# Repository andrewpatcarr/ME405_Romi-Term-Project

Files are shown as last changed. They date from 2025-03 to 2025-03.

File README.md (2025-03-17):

# ME-405 Romi Term Project
### By: Andrew Carr and Alain Kanadjian
### Instructor: Charlie Refvem

---

This repository houses all documentation regarding our Romi project 
that was worked on throughout this quarter.

All documentation can be found here:

[ME-405 Romi Term Project Documentation](https://andrewpatcarr.github.io/ME405_Romi-Term-Project/)

### The Project

Throughout our quarter in ME-405, we worked on labs that used our mini-car robot, Romi, in different ways. 
We parameterized our motors, implemented task-based non-blocking programming, implemented an IR line sensor, and worked with an IMU. 
All of these labs were building towards our term project/challenge.

romi_pic

We were tasked with completing a complex track with obstacles, quick bends, and varying surface prints. 

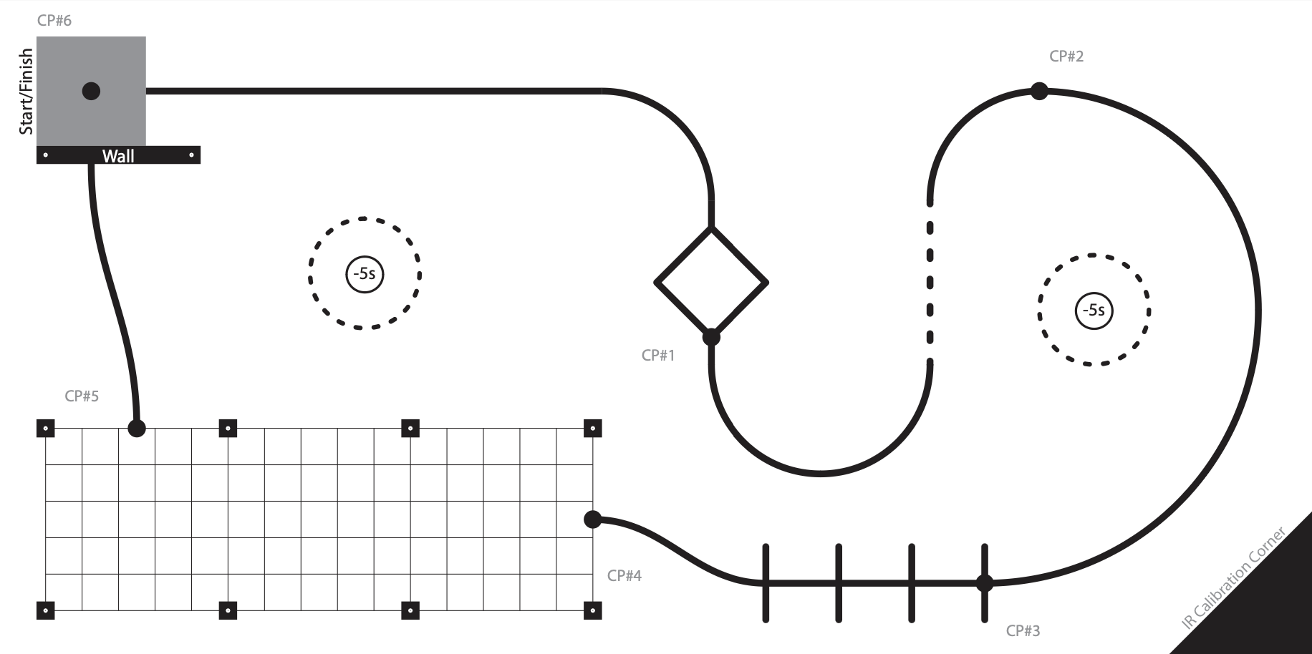
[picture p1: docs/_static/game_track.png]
Game Track


### Hardware

Our Pololu Romi has a STM-32 Nucleo with a Calpoly custom 'Shoe of Brian' along with a Pololu motor driver.

Romi has two DC motor driven wheels with quadrature encoders. We mounted an IMU for orientation sensing, 
an IR sensor to track a black line, and a bump sensor for impact sensing.

See cad and pinout folders for files and the [hardware](https://andrewpatcarr.github.io/ME405_Romi-Term-Project/hardware.html)
and [assembly](https://andrewpatcarr.github.io/ME405_Romi-Term-Project/assembly.html) pages for documentation.

### Programming

We structured our code using object-oriented programming principles and task-based architecture for
streamlined modifications and control. Each part of the robot runs as a separate task, allowing for easy 
debugging and organization. We use a PI controller to set motor speed based on encoder feedback. 
The encoder uses quadrature signals and an AR reset to prevent overflow. Our IR sensor uses a centroid-based 
algorithm to track black lines for navigation.

See the source code in the code folder and the [programming](https://andrewpatcarr.github.io/ME405_Romi-Term-Project/programming.html),
[control](https://andrewpatcarr.github.io/ME405_Romi-Term-Project/control_scheme.html), and
[code modules](https://andrewpatcarr.github.io/ME405_Romi-Term-Project/code_rst/modules.html) pages for detailed documentation.

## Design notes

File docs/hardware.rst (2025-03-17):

Hardware
========

Components
----------

.. list-table::
   :widths: 50 20 50
   :header-rows: 1

   * - Item
     - Quantity
     - Notes
   * - `Romi Chassis Kit <https://www.pololu.com/category/203/romi-chassis-kits>`_
     - 1
     - A differential-drive mobile robot platform.
   * - `Romi Ball Caster Kit <https://www.pololu.com/category/204/romi-chassis-components>`_
     - 1
     - Provides a third point of contact for the robot.
   * - `Snap-Action Switch with 18.5mm Bump Lever <https://www.pololu.com/product/1405>`_
     - 1
     - A single-pole, double-throw momentary switch used as a tactile bump sensor for physical collisions.
   * - `QTR-HD-13A Reflectance Sensor Array <https://www.pololu.com/product/4213>`_
     - 1
     - A 13-channel array of IR LED/phototransistor pairs with 4mm length, used for precise line detection and following.
   * - `Gearmotor and Encoder Assembly for Romi/TI-RSLK MAX <https://www.pololu.com/product/3675>`_
     - 2
     -  Gearmotors with encoders pre-installed, providing feedback for precise motor control
   * - `Adafruit BNO055 IMU <https://learn.adafruit.com/adafruit-bno055-absolute-orientation-sensor/overview>`_
     - 1
     - 9-DOF absolute orientation sensor
   * - `STM32 NUCLEO-L476RG <https://www.st.com/en/evaluation-tools/nucleo-l476rg.html>`__
     - 1
     - Microcontroller Dev Board

Romi
----
Romi is a small differential drive robot that uses two wheels powered by DC
motors with encoders. Romi has a Shoe of Brian and Nucleo-L476RG along with
attached components like a bump sensor, QTR sensor, and IMU. The plastic
chassis is lightweight allowing easier configuration and navigation. The
two DC motors are connected to a gearbox for proper torque, controlled by
pulse width modulation signals, allowing for variable speed control. The
encoders connected to the motors allow for a closed feedback loop, so we
can implement motion tracking and autonomous movement. The motor driver
controls the voltage and current to each motor, allowing for bidirectional
movement and speed control.

To help control each motor, we ran step input tests to find different characteristics of the motors.

Example Plots (Right Motor)
---------------------------

Position vs Time at different open loop step inputs

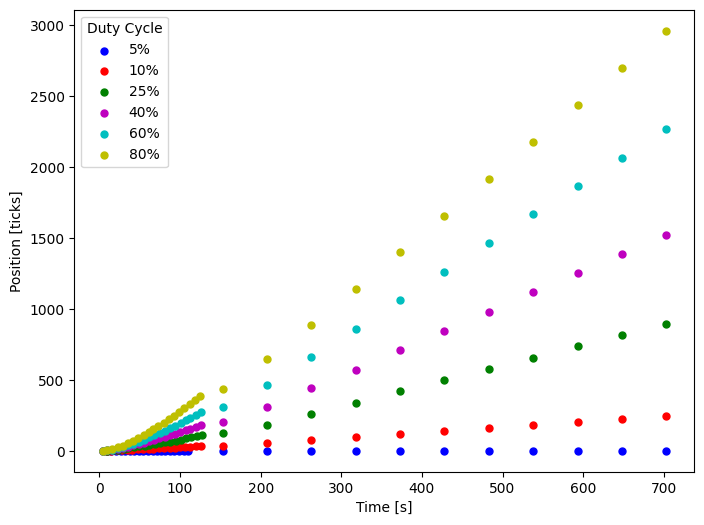
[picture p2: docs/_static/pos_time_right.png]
pos_time_right


Velocity vs Time at different open loop step inputs

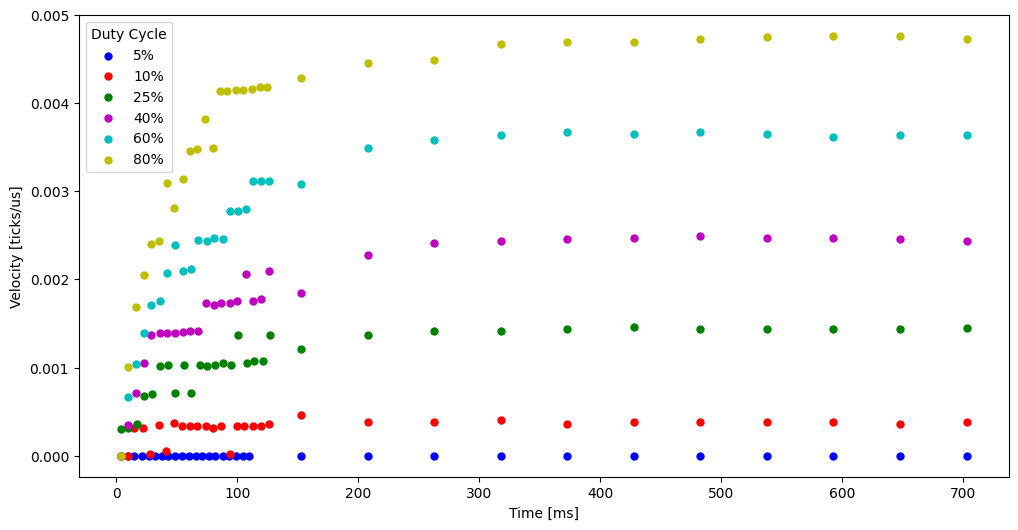
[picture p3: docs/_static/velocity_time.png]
velocity_time


Steady-State Velocity vs Input Voltage

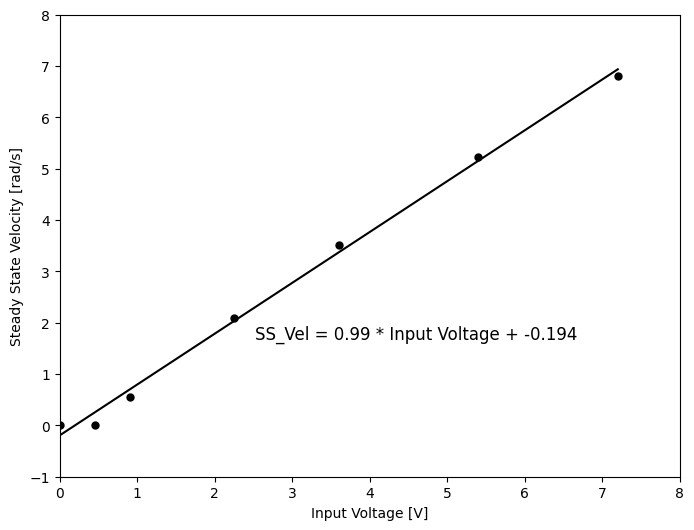
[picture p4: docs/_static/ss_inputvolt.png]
ss_inputvolt


Linearized Velocity vs Time (inverse of slope gives time constant)

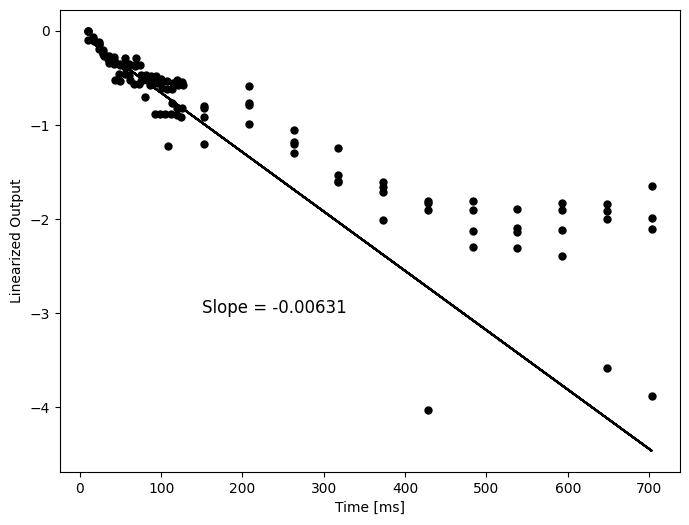
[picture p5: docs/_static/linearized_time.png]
linearized_time


Motor Parameters
----------------

.. list-table::
   :widths: 20 40 30 40
   :header-rows: 1

   * - Motor
     - Time Constant [ms]
     - Gain [deg/s]
     - Startup PWM %
   * - Right
     - 158
     - 56.7
     - 2.77
   * - Left
     - 170
     - 60.3
     - 6.48

STM-32 Nucleo
-------------
Our Romi uses a STM32 Nucleo (particularly the `NUCLEO-L476RG <https://www.st.com/en/evaluation-tools/nucleo-l476rg.html>`_)
as its microcontroller. The board has an ARM processor, various GPIO pins,
and interfaces for I2C, SPI, and UART. The Nucleo allows for real time data processing, sensor
integration and motor control through MicroPython.

QTR Sensor
----------
The QTR sensor has an array of infrared reflectance sensor for line following, consisting of an IR LED
and phototransistor to detect reflectance of the surface it is pointed at. White surfaces return low readings,
while black surfaces return high readings. This sensor helps ROMI implement PID line following, adjusting motor
speeds based on intensity of reflected light to the sensor.

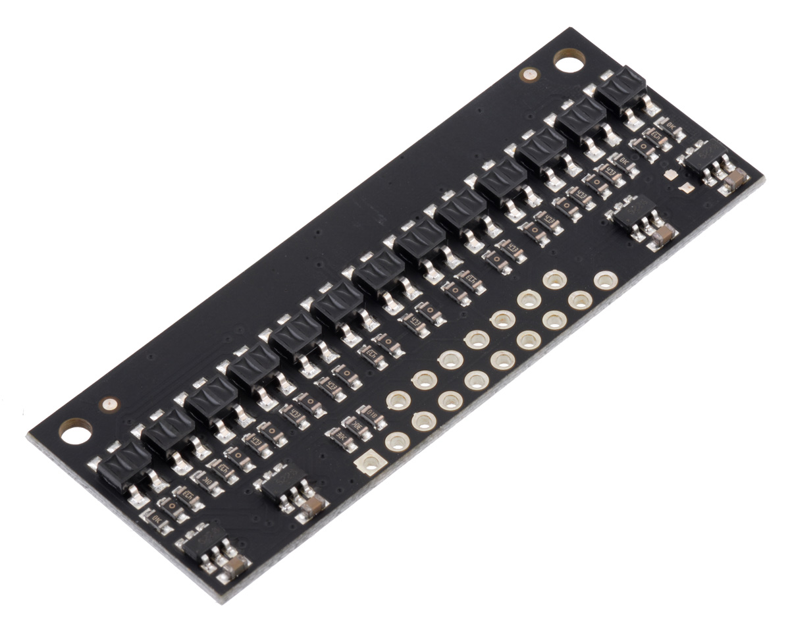
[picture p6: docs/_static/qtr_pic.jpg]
QTR Sensor


Image used from `pololu.com <https://a.pololu-files.com/picture/0J9915.1200.jpg?cc7523ea26737e153f8346b5d38e696a>`_.

IMU
---
We use an inertial measurement unit to track acceleration, angular velocity, and magnetic field heading.
Romi uses a BNO055 from adafruit which is a 9-DOF absolute orientation sensor using an accelerometer,
gyroscope and a magnetometer. This allows us to track orientation, follow angles relative to north,
and any environmental disturbances. We use I2C to communicate between our microcontroller and the IMU.

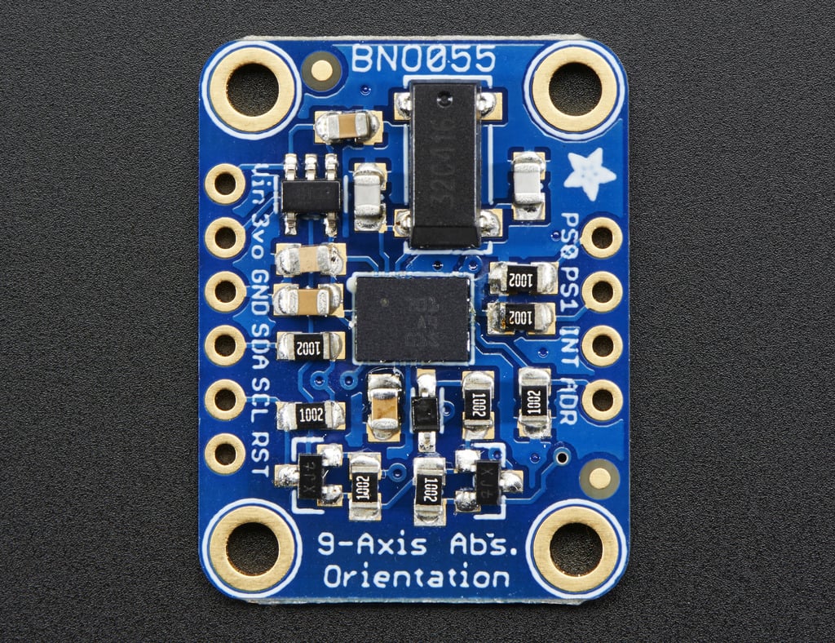
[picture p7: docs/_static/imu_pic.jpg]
IMU


Image used from `adafruit.com <https://learn.adafruit.com/assets/24585>`_.

Bump Sensor
-----------
The bump sensor uses a gate switch to detect physical collisions in the robot's path. We integrated the sensor
using a 3D printed part. When the bump sensor is activated, it sends a signal to the microcontroller, which when
then have the robot react to its situation. In the course, this meant the robot would reverse before going around
the wall. This adds another sense to our robot which is essential to navigate the final course.

Bump Sensor CAD
---------------

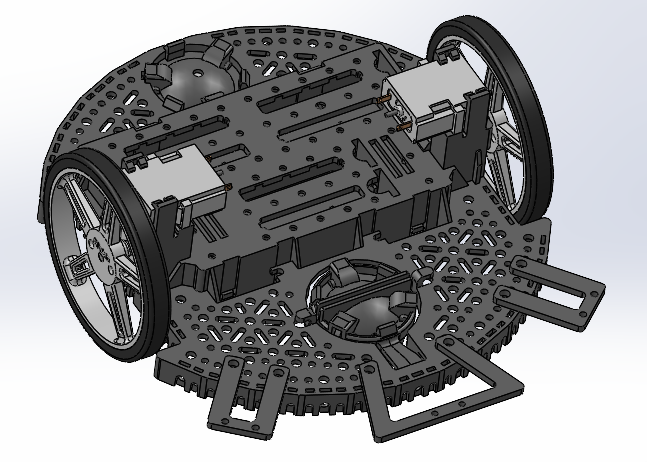
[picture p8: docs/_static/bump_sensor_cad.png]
Bump Sensor CAD


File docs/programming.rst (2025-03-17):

Programming
===========

Written in micropython, our codebase is devised of scheduler based tasks written as finite state machines
with shared variables. Each peripheral has its own class with task class to handle its integration.

Tasks
-----

We use Cal Poly's `ME405-Support libraries <https://spluttflob.github.io/ME405-Support/index.html>`_
which provide the python files for implementation of tasks, shares and queues. This allows us to time
when we get sensor readings, drive motors and use our controller. Shares allow us to have variables
that different tasks can use and change. For example, our controller task can adjust the motor speed
share which the motor task reads and uses to drive the motors to achieve a goal.

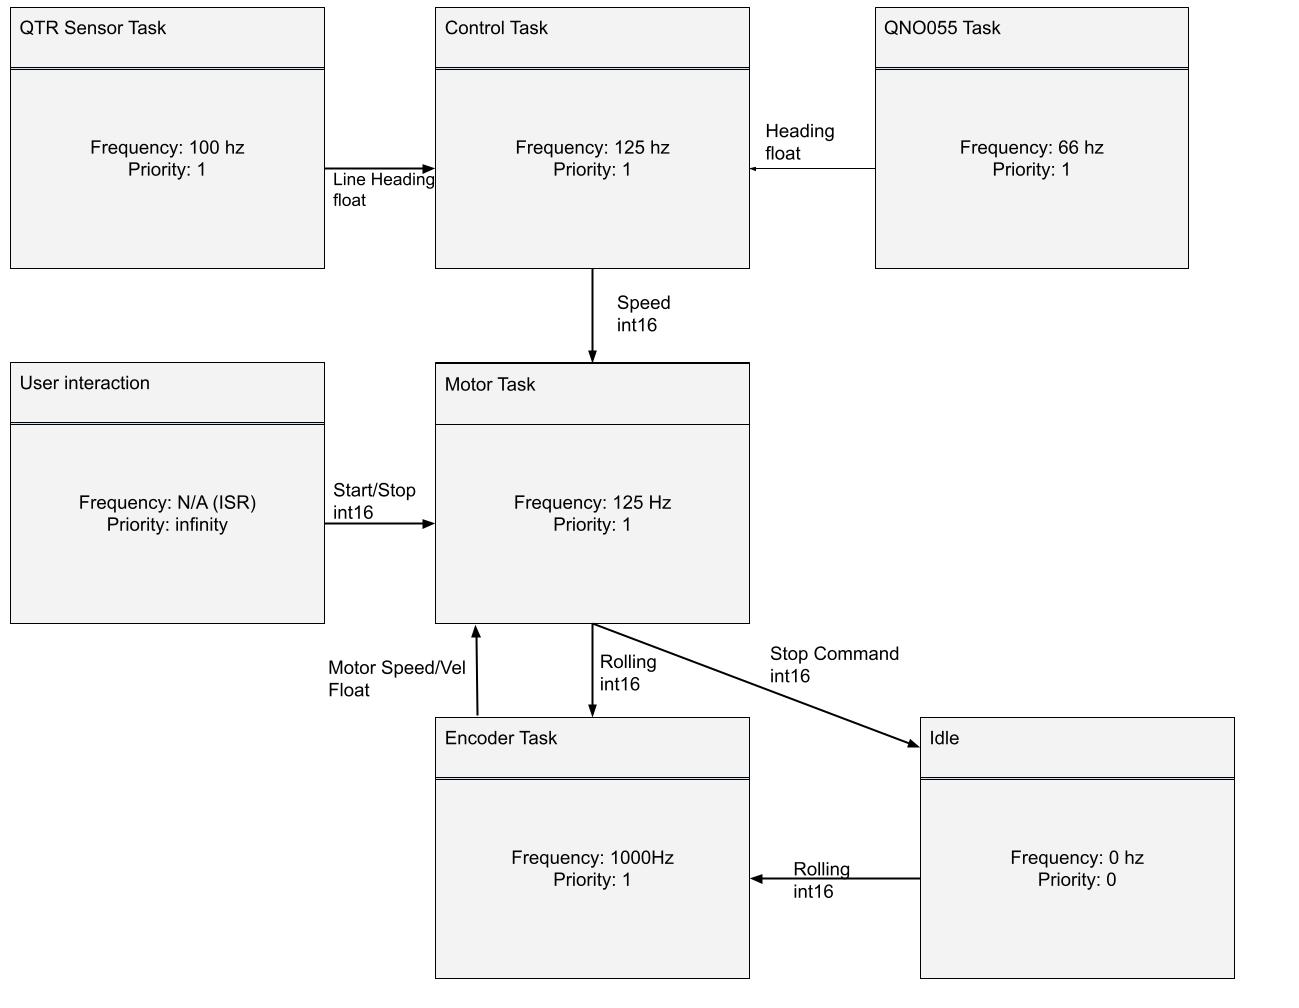
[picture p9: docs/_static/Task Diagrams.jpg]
Task Diagram for Task Scheduler


Shares
------

.. list-table::
   :widths: 30 20 70
   :header-rows: 1

   * - Shared Variable
     - Data Type
     - Purpose
   * - right_pos
     - signed float
     - Encoder position in ticks of right motor
   * - left_pos
     - signed float
     - Encoder position in ticks of left motor
   * - right_vel
     - signed float
     - Velocity of right motor in ticks/us
   * - left_vel
     - signed float
     - Velocity of left motor in ticks/us
   * - right_speed
     - signed int
     - Desired direction and PWM % of right motor
   * - left_speed
     - signed int
     - Desired direction and PWM % of left motor
   * - right_stop
     - signed int
     - Value of stop state of right motor (0 on, 1 off)
   * - left_stop
     - signed int
     - Value of stop state of left motor (0 on, 1 off)
   * - line_error
     - signed float
     - Error value of black line under line sensor
   * - heading
     - signed float
     - Current heading reading from IMU in degrees
   * - heading_set
     - signed float
     - Desired heading angle in degrees
   * - line_heading
     - signed int
     - Value determining controller state, (0, line following; 1 or -1 (reverse), heading following; 2, in place heading following
       (turn); 3, straight reverse; 4, stop)

Finite State Machines
---------------------

Each our tasks use generators written as finite state machines (FSM)
Idk why but this FSM isnt updating from old jpg

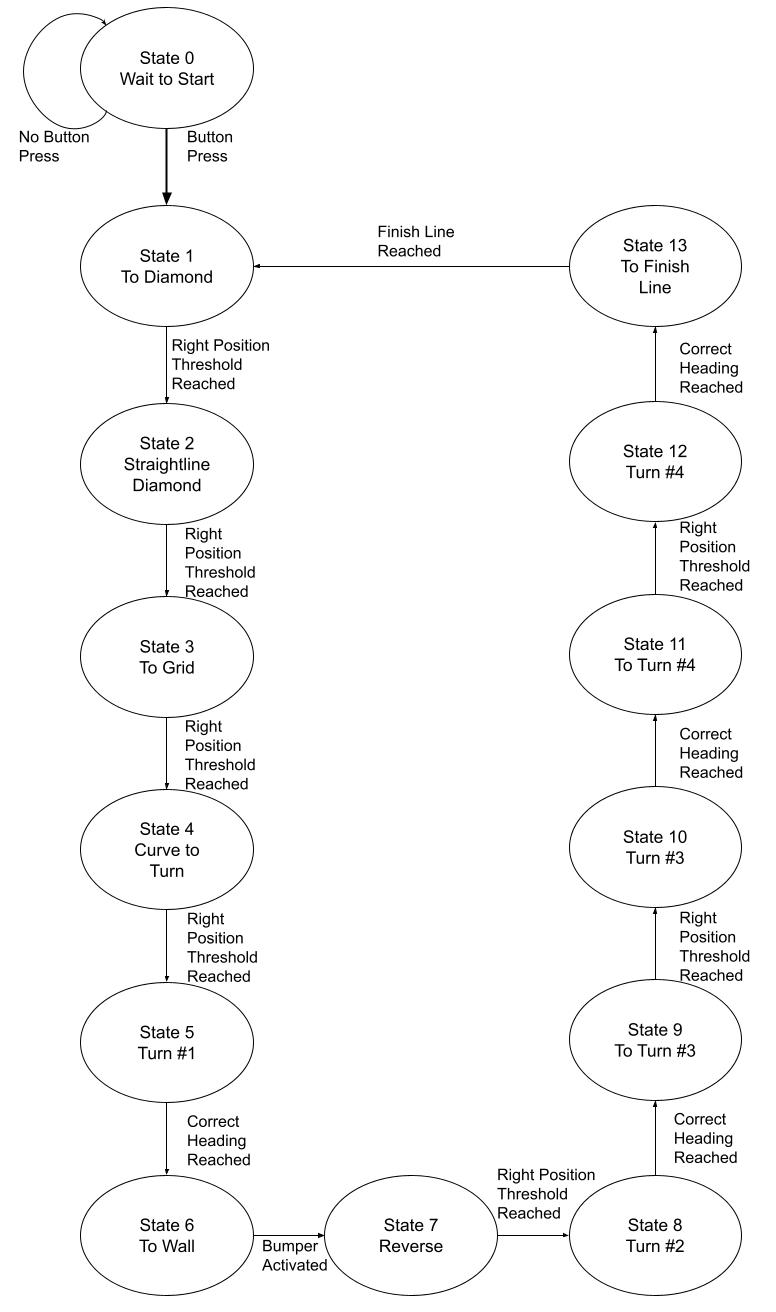
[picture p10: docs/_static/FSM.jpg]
Finite State Machine for main.py


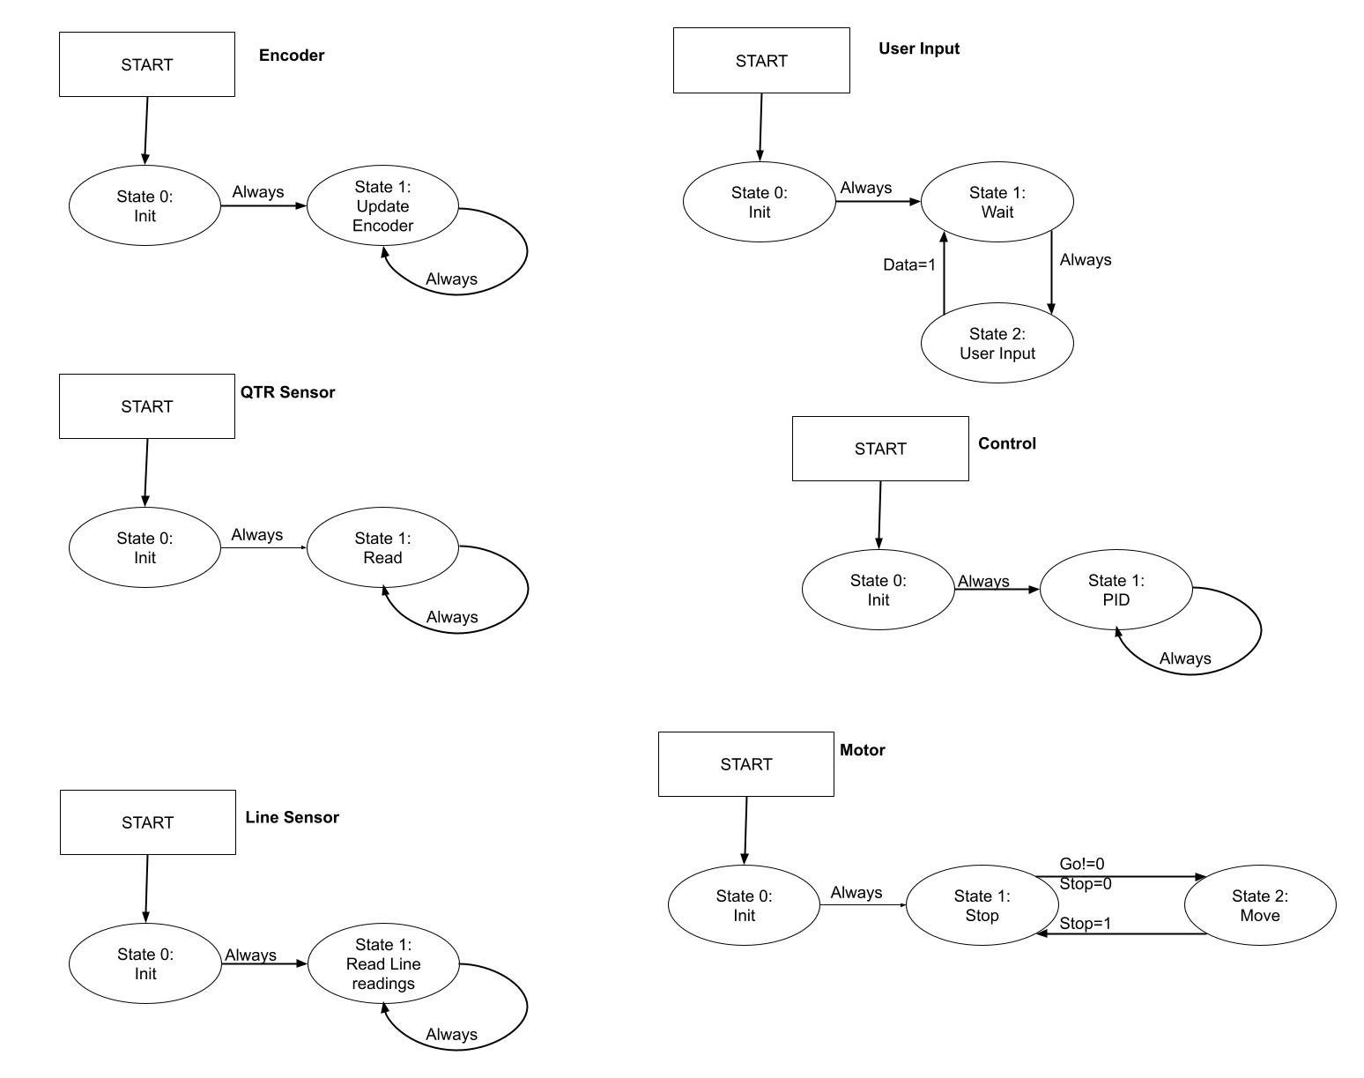
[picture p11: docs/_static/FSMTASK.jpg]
Finite State Machine for Task scheduler


In main, we use a FSM to complete the course. It features hardcoded encoder position thresholds which jump between
line following, heading following and full reverse modes.

Course FSM
----------

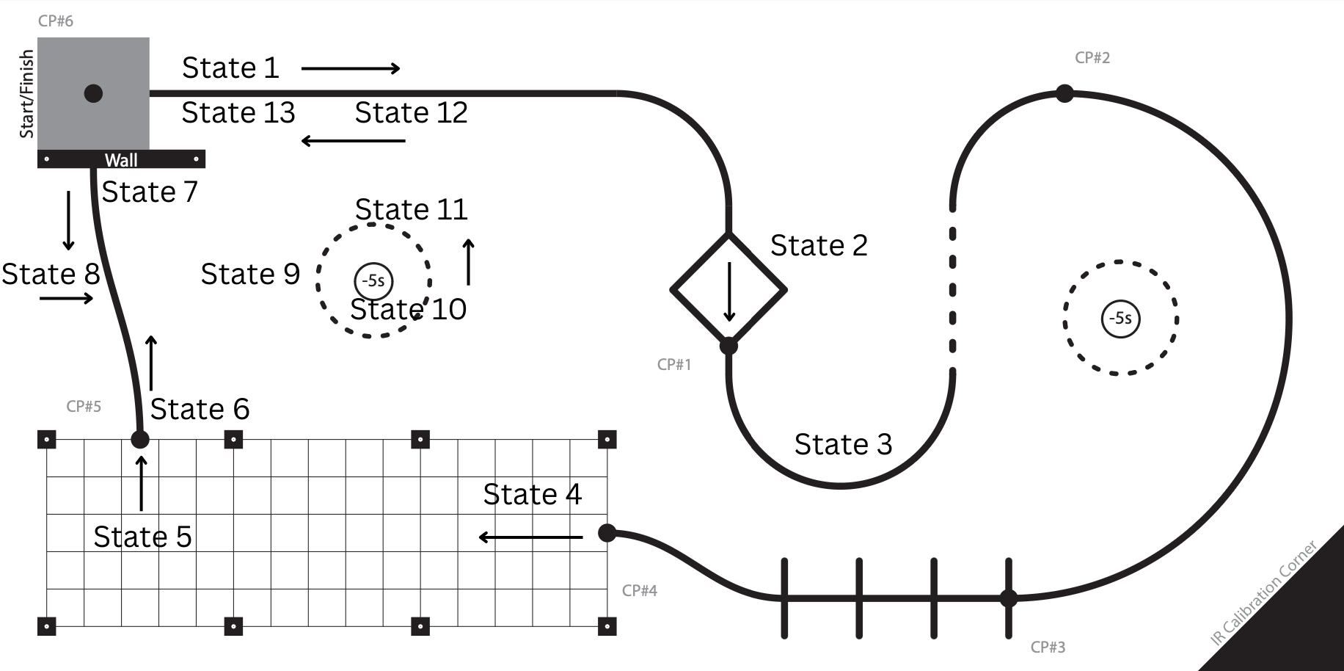
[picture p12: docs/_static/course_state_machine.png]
course_state_machine


Line Sensing Methods
--------------------

Our line sensor features an array of light sensor that all produce a reading that can be normalized to 0 to 1 with a
1 being black. If the line is perfectly below the sensor, we get a 'normal' distribution with the middle sensors
reporting a 1 while each sensor moving outwards has less black line under it. We use this theory to find the
centroid of our sensor array which we can compare to the centroid of a perfectly centered line.

.. math::
    x = \frac{\sum_{i}q_i x_i}{\sum_{i}q_i}

where  :math:`q_i` is the sensor value and :math:`x_i` is the sensor location

This is sent to our controller which tells the motors what to do to realign the robot with line.

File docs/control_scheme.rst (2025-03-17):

Control
=======

Our Romi is a relatively linear system with mostly simple sensors which points us to the
ever-reliable PID controller. Due to the noise of most of our signals, we decided to use PI control. However, during
testing, a well tuned proportional controller was good enough. If we had more time and were tasked to optimize our time
on the course, we would implement integral control to reduce the jumpyness and steady state error we sometimes
experienced.

We have a cascading control scheme that closes the loop with multiple sensors.
Our controller starts with a path pointing sensor such as our line sensor or the heading
reading from our IMU. This signal is processed to tell each motor what speed it should
go to achieve the goal of our outmost controller.

The speeds that are sent to the
motors are monitored by another controller via the encoder. This allows us to accurately
follow a line, go in a straight line and individually tune each system.

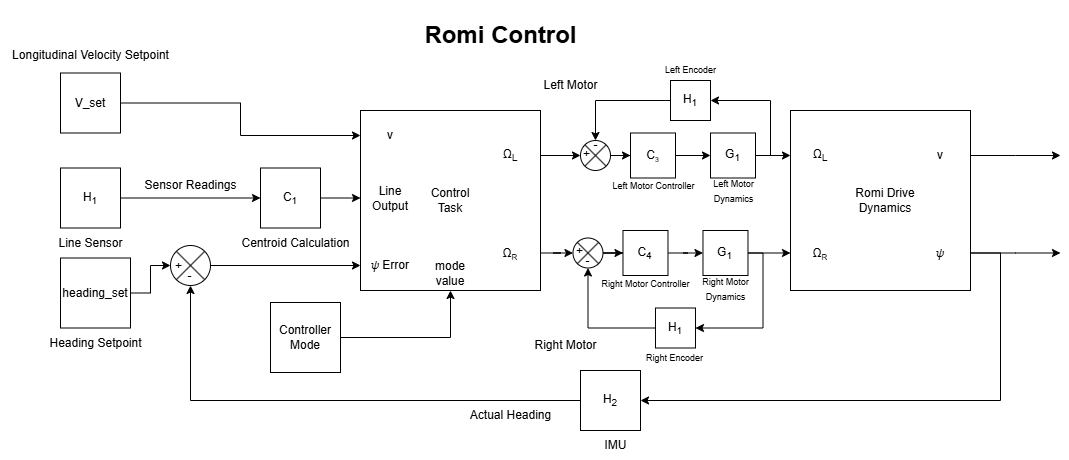
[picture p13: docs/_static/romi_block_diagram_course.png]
ControlBlockDiagram


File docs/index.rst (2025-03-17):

.. ME-405 Term Project documentation master file, created by
   sphinx-quickstart on Sat Mar  8 17:24:39 2025.
   You can adapt this file completely to your liking, but it should at least
   contain the root `toctree` directive.

ME-405 Term Project Documentation
=================================
**By: Andrew Carr and Alain Kanadjian**

**Instructor: Charlie Refvem**

The Project - Romi
------------------

Throughout the quarter in ME-405, we worked on labs that built, wired, and programmed our mini-car robot, Romi, in different ways
for different tasks.

romi_pic_cropped

We parameterized our motors, implemented task-based non-blocking programming, implemented an IR line sensor,
and worked with an IMU. All of these labs were building towards our term project/challenge. We needed to complete
the following course by hitting each checkpoint, detecting the wall and making our way back to the start pad.

Course
------

GameTrack

Successful Run
--------------

After many many trials, debugging, reworking control methods, hardcoding distances, we were able to complete the course.

.. youtube:: lIelwNlQIkY
   :width: 510
   :height: 907

(Yes, we barely made it back on the pad but we are counting it :))

In this documentation, we will talk about the hardware and software used in our Romi. There is documentation regarding how our programs,
the drivers we created for each component, and the controllers we implemented.

Contents
--------

.. toctree::
   :maxdepth: 2

   hardware.rst
   assembly.rst
   control_scheme.rst
   programming.rst
   code_rst/modules

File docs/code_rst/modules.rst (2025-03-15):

Code Modules
============

.. toctree::
   :maxdepth: 4

   BNO055
   control_task
   cotask
   encoder
   encoder_task
   heading_task
   main
   motor
   motor_task
   qtr_sensor
   task_share

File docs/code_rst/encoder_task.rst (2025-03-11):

encoder\_task
=============

.. automodule:: encoder_task
   :members:
   :show-inheritance:
   :undoc-members:

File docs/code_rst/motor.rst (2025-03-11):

motor
=====

.. automodule:: motor
   :members:
   :show-inheritance:
   :undoc-members:

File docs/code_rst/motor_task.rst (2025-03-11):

motor\_task
===========

.. automodule:: motor_task
   :members:
   :show-inheritance:
   :undoc-members:

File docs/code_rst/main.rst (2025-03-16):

main
====

Our main program initializes all class objects, tasks and shares. It then runs the scheduler
and jumps between states to complete the course.

Course Finite State Machine
...........................

.. code-block:: python

    print('Press button to start run')

    try:
        while True:
            cotask.task_list.pri_sched()
            """Print Section"""
            now = ticks_ms()
            if ticks_diff(deadline, now) < 0:
                print(
                    f'Right_Pos- thresh: {right_pos.get() - thresh}, State: {state}, R_speed: {right_speed.get()}, Heading: {heading.get()}')
                deadline = ticks_add(deadline, interval)

            """Course State machine

            Hardcoded states based on encoder position and bumper state.
            Jumps between line sensing and north sensing modes to complete the course.
            """

            if state == S0_wait_to_start:
                line_heading.put(4)
                if button_state != prev_button_state:
                    prev_button_state = button_state
                    sleep(.2)
                    state = S1_to_diamond
            elif button_state != prev_button_state:
                prev_button_state = button_state
                state = S0_wait_to_start

            if state == S1_to_diamond:
                line_heading.put(0)
                if rep == 0:
                    thresh = right_pos.get() + 5_500
                    heading_north = (imu.read_heading()+90)%360
                    print(f'Heading North: {heading_north}')
                    rep += 1

                if right_pos.get() > thresh:
                    state = S2_straightline_diamond
                    rep = 0

            if state == S2_straightline_diamond:

                if rep == 0:
                    line_heading.put(1)
                    hed_set = heading_north + 90

                    if hed_set < 0:
                        hed_set += 360
                    elif hed_set > 360:
                        hed_set -= 360
                    heading_set.put(hed_set)
                    thresh = right_pos.get() + 1_000
                    print(f'Threshold: {thresh}, hed_set: {hed_set}')
                    rep += 1
                if right_pos.get() > thresh:
                    state = S3_to_grid
                    rep = 0
            if state == S3_to_grid:
                line_heading.put(0)
                if rep == 0:
                    thresh = right_pos.get() + 16_000
                    rep += 1
                if right_pos.get() > thresh:
                    state = S4_to_turn
                    rep = 0
            if state == S4_to_turn:
                line_heading.put(1)
                if rep == 0:
                    thresh = right_pos.get() + 4_000
                    hed_set = heading_north - 180
                    if hed_set < 0:
                        hed_set += 360
                    elif hed_set > 360:
                        hed_set -= 360
                    heading_set.put(hed_set)
                    rep += 1
                if right_pos.get() > thresh:
                    state = S5_turn_1
                    right_speed.put(0)
                    left_speed.put(0)
                    rep = 0
            if state == S5_turn_1:
                if rep == 0:
                    hed_set = heading_north - 90
                    if hed_set < 0:
                        hed_set += 360
                    elif hed_set > 360:
                        hed_set -= 360
                    heading_set.put(hed_set)
                    line_heading.put(2)
                    rep += 1
                if -10 < (hed_set - heading.get()) < 10:
                    right_speed.put(0)
                    left_speed.put(0)
                    state = S6_to_wall
                    rep = 0
            if state == S6_to_wall:
                line_heading.put(0)
                if bumper_state:
                    print(f'Bumper hit')
                    right_speed.put(0)
                    left_speed.put(0)
                    state = S7_reverse
            if state == S7_reverse:
                line_heading.put(3)

                if rep == 0:
                    thresh = right_pos.get() - 500
                    hed_set = heading_north - 90

                    if hed_set < 0:
                        hed_set += 360
                    elif hed_set > 360:
                        hed_set -= 360
                    print(f'hed_set: {hed_set}')
                    heading_set.put(hed_set)
                    rep += 1
                if right_pos.get() < thresh:
                    right_speed.put(0)
                    left_speed.put(0)
                    state = S8_turn_2
                    rep = 0
            if state == S8_turn_2:
                line_heading.put(2)
                if rep == 0:
                    hed_set = heading_north
                    if hed_set < 0:
                        hed_set += 360
                    elif hed_set > 360:
                        hed_set -= 360
                    heading_set.put(hed_set)
                    line_heading.put(2)
                    rep += 1
                if -10 < (hed_set - heading.get()) < 10:
                    right_speed.put(0)
                    left_speed.put(0)
                    state = S9_to_3
                    rep = 0
            if state == S9_to_3:
                line_heading.put(1)
                heading_set.put(heading_north)
                if rep == 0:
                    thresh = right_pos.get() + 2_000
                    rep += 1
                if right_pos.get() > thresh:
                    state = S10_turn_3
                    rep = 0
            if state == S10_turn_3:
                line_heading.put(2)
                if rep == 0:
                    hed_set = heading_north - 90
                    if hed_set < 0:
                        hed_set += 360
                    elif hed_set > 360:
                        hed_set -= 360
                    heading_set.put(hed_set)
                    line_heading.put(2)
                    rep += 1
                if -10 < (hed_set - heading.get()) < 10:
                    right_speed.put(0)
                    left_speed.put(0)
                    state = S11_to_4
                    rep = 0
            if state == S11_to_4:
                line_heading.put(1)
                hed_set = heading_north - 90
                if hed_set < 0:
                    hed_set += 360
                elif hed_set > 360:
                    hed_set -= 360
                heading_set.put(hed_set)
                if rep == 0:
                    thresh = right_pos.get() + 2_000
                    rep += 1
                if right_pos.get() > thresh:
                    state = S12_turn_4
                    rep = 0
            if state == S12_turn_4:
                line_heading.put(2)
                if rep == 0:
                    hed_set = heading_north - 180
                    if hed_set < 0:
                        hed_set += 360
                    elif hed_set > 360:
                        hed_set -= 360
                    heading_set.put(hed_set)
                    line_heading.put(2)
                    rep += 1
                if -10 < (hed_set - heading.get()) < 10:
                    right_speed.put(0)
                    left_speed.put(0)
                    state = S13_to_finish
                    rep = 0
            if state == S13_to_finish:
                if rep == 0:
                    hed_set = heading_north - 180
                    if hed_set < 0:
                        hed_set += 360
                    elif hed_set > 360:
                        hed_set -= 360
                    heading_set.put(hed_set)
                    line_heading.put(1)
                    thresh = right_pos.get() + 2_200
                    rep += 1
                if right_pos.get() > thresh:
                    state = S0_wait_to_start
                    rep = 0

                    print('Done!')

.. automodule:: main
   :members:
   :show-inheritance:
   :undoc-members:

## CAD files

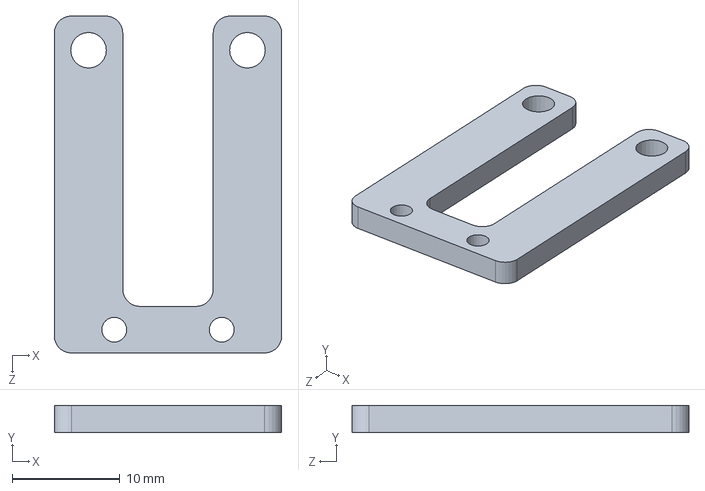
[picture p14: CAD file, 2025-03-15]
cad/Side Bump Sensor Mount.SLDPRT
21.1 x 2.54 x 31.2 mm

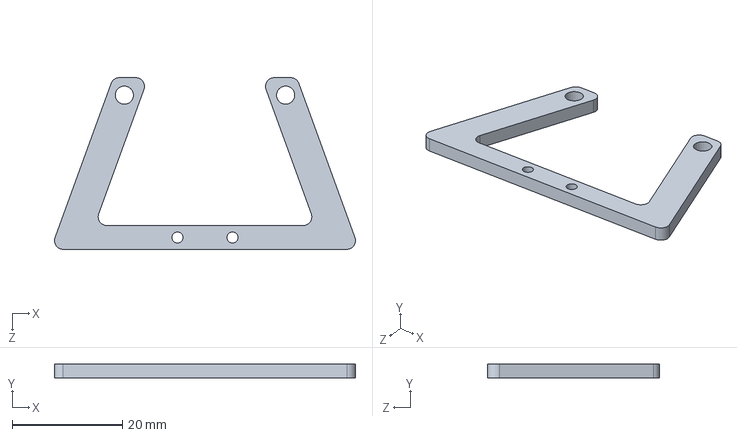
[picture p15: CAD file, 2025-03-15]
cad/Front Bump Sensor Mount.SLDPRT
54.5 x 2.54 x 31.1 mm

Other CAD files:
cad/STLs/Front Bump Sensor Mount.STL
cad/STLs/Side Bump Sensor Mount.STL

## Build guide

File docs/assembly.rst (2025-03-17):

Assembly
========

Everything is bolted together with each component being designed to work well. Our QTR sensor is placed very close
to the ground for the most accurate and reliable reading. The bump sensor is bolted in out in front of the Romi.

Pinout
------

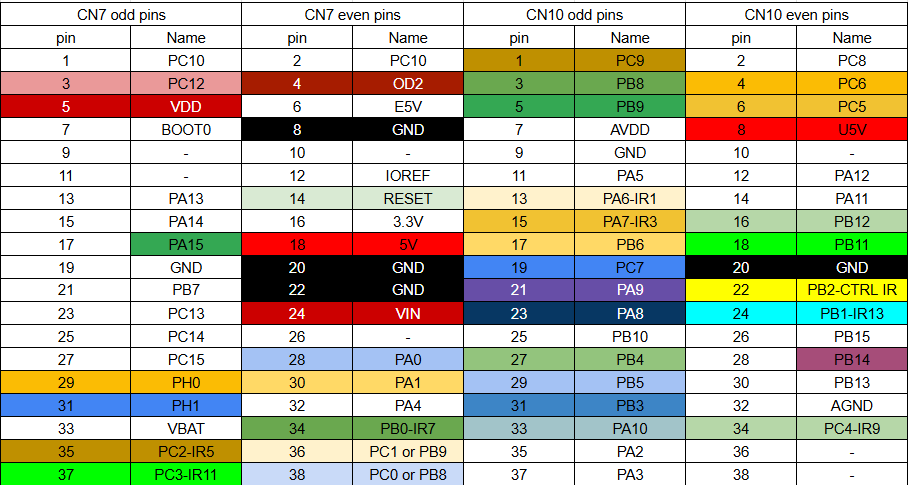
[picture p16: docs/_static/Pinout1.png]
Pinout using our STM32 Nucleo Board

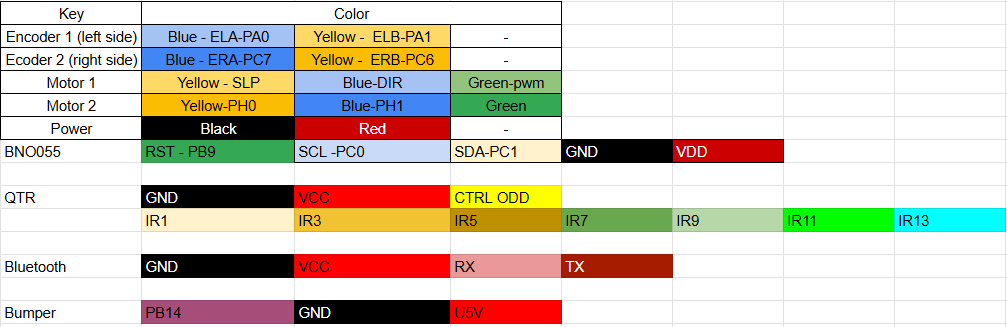
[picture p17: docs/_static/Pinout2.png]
Pinout of components by color


These are the pinouts pertaining to the components and STM32 Nucleo Board.

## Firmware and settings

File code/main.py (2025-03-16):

from pyb import Pin, Timer, millis, USB_VCP, UART, ADC, I2C, Switch, ExtInt
from time import ticks_us, ticks_diff, ticks_add, sleep, time, ticks_ms
import math
from motor import Motor
import cotask
import task_share
from encoder_task import EncoderTask
from motor_task import MotorTask
from qtr_sensor import QTRSensor, QTRTask
from control_task import ControlTask
from heading_task import HeadingTask
from BNO055 import BNO055

"""Motor Pin Definitions"""

right_pwm_pin = "B9"
right_dir_pin = "H1"
right_slp_pin = "H0"
right_enc_A = "C7"
right_enc_B = "C6"
right_enc_timer = 8
right_pwm_timer = 4

left_pwm_pin = "B4"
left_dir_pin = "B5"
left_slp_pin = "B6"
left_enc_A = "A0"
left_enc_B = "A1"
left_enc_timer = 2
left_pwm_timer = 3

"""QTR Sensor Pin Definitions"""

ir_1 = 'A6'
ir_3 = 'A7'
ir_5 = 'C2'
ir_7 = 'B0'
ir_9 = 'C4'
ir_11 = 'C3'
ir_13 = 'B1'
ir_ctrl = 'B2'

"""Button Interrupt Creation"""

user_button_pin = 'C13'
button = Pin(user_button_pin, Pin.IN, Pin.PULL_UP)
sw_1 = Switch()
prev_button_state = False
button_state = False


def button_pushed():
    """A function for handling the user button inputs"""
    global button_state
    button_state = not button_state
    sleep(.200)  # Debouncing delay


sw_1.callback(button_pushed)


def wait_for_button():
    """A blocking user input function used to do calibration and to start the course"""
    global button_state, prev_button_state
    while True:
        if button_state != prev_button_state:
            prev_button_state = button_state
            break



enc_pins = [right_enc_A, right_enc_B, right_enc_timer, left_enc_A, left_enc_B, left_enc_timer]
motor_pins = [right_pwm_pin, right_dir_pin, right_slp_pin, right_pwm_timer, left_pwm_pin, left_dir_pin, left_slp_pin,
              left_pwm_timer]
qtr_pins = [ir_1, ir_3, ir_5, ir_7, ir_9, ir_11, ir_13]

"""Create motor objects to stop motors from initial movement."""

right_motor = Motor([right_pwm_pin, right_dir_pin, right_slp_pin, right_pwm_timer], 4, [1, 0])
left_motor = Motor([left_pwm_pin, left_dir_pin, left_slp_pin, left_pwm_timer], 1, [1, 0])
right_motor.stop()
left_motor.stop()

"""Initialize i2c3"""

i2c = I2C(3, I2C.CONTROLLER)  # Make sure you're using the correct I2C bus
sleep(1)  # Allow devices to power up

"""Bumper Interrupt Creation"""

bumper_pin = Pin('B14', Pin.IN, Pin.PULL_UP)
prev_bumper_state = False
bumper_state = False
last_interrupt_time = 0  # Stores the last trigger time
debounce_delay = 50  # Debounce delay in milliseconds


def bumper_pushed(line):
    """A function for handling the bumper inputs"""
    global bumper_state, last_interrupt_time
    current_time = millis()  # Get current time in ms
    if (current_time - last_interrupt_time) > debounce_delay:  # Check debounce
        bumper_state = True
        last_interrupt_time = current_time  # Update last trigger time


bumper_inter = ExtInt(bumper_pin, ExtInt.IRQ_FALLING, Pin.PULL_UP, bumper_pushed)

"""Create Sensor and Task Objects"""

encoder = EncoderTask(enc_pins)
motor = MotorTask(motor_pins[0:4], motor_pins[4:8], 4, 1, [.7, 0], [.9, 0])
qtr = QTRSensor(qtr_pins, ir_ctrl)
qtr_more = QTRTask(qtr)
control = ControlTask([18, 0, 0], 0)  # [k_p, k_i, K_d], offset
imu = BNO055(i2c, 'A15')
imu_more = HeadingTask(imu)

if __name__ == '__main__':
    """Create shares"""
    right_pos = task_share.Share('f', name='Right Encoder Pos')
    left_pos = task_share.Share('f', name='Left Encoder Pos')
    right_vel = task_share.Share('f', name='Right Encoder Vel')
    left_vel = task_share.Share('f', name='Left Encoder Vel')
    right_speed = task_share.Share('h', name="Right Speed")  # Input Speed for motor pwm [%]
    right_stop = task_share.Share('h', name="Right Stop")
    left_speed = task_share.Share('h', name="Left speed")  # Input Speed for motor pwm [%]
    left_stop = task_share.Share('h', name="Left Stop")
    line_error = task_share.Share('f', name="Error")
    heading = task_share.Share('f', name="Heading")
    line_heading = task_share.Share('h', name="Line Switch")
    heading_set = task_share.Share('f', name="Heading Set")

    """Create Tasks"""
    enc_task = cotask.Task(encoder.encoder_gen, name='Encoder Task', priority=1, period=1,
                           shares=([right_pos, right_vel, left_pos, left_vel]), trace=False, profile=True)

    motor_task = cotask.Task(motor.go, name='Motor Task', priority=1, period=8,
                             shares=([right_speed, left_speed, right_stop, left_stop, right_vel, left_vel]),
                             trace=False, profile=True)
    controller_task = cotask.Task(control.controller, name='Control Task', priority=1, period=8,
                                  shares=[line_error, right_speed, left_speed, line_heading, heading, heading_set],
                                  trace=False, profile=True)
    qtr_task = cotask.Task(qtr_more.get_line, name='QTR Task', priority=1, period=10, shares=line_error, trace=False,
                           profile=True)
    imu_task = cotask.Task(imu_more.get_heading, name='IMU Task', priority=1, period=15, shares=heading, trace=False,
                           profile=True)

    """Add Tasks to cotask task list"""
    cotask.task_list.append(enc_task)
    cotask.task_list.append(qtr_task)
    cotask.task_list.append(controller_task)
    cotask.task_list.append(motor_task)
    cotask.task_list.append(imu_task)

    """Put motor in stopped mode"""
    right_speed.put(0)
    right_stop.put(1)
    left_speed.put(0)
    left_stop.put(1)

    """Calibration (if needed)"""
    # print('place on white')
    # wait_for_button()
    # qtr.calibrate_white()
    #
    # print('place on black')
    # wait_for_button()
    # qtr.calibrate_black()

    """Print timing initialization"""
    interval = 500
    begin_time = ticks_ms()
    deadline = ticks_add(begin_time, interval)

    """Take motors out of stop mode"""
    right_stop.put(0)
    left_stop.put(0)

    """Course State Machine Definitions"""
    state = 0
    S0_wait_to_start = 0
    S1_to_diamond = 1
    S2_straightline_diamond = 2
    S3_to_grid = 3
    S4_to_turn = 4
    S5_turn_1 = 5
    S6_to_wall = 6
    S7_reverse = 7
    S8_turn_2 = 8
    S9_to_3 = 9
    S10_turn_3 = 10
    S11_to_4 = 11
    S12_turn_4 = 12
    S13_to_finish = 13

    thresh = 0
    rep = 0
    heading_north = 0
    hed_set = 0

    print('Press button to start run')

    try:
        while True:
            cotask.task_list.pri_sched()
            """Print Section"""
            now = ticks_ms()
            if ticks_diff(deadline, now) < 0:
                print(
                    f'Right_Pos- thresh: {right_pos.get() - thresh}, State: {state}, R_speed: {right_speed.get()}, Heading: {heading.get()}')
                deadline = ticks_add(deadline, interval)

            """Course State machine
            
            Hardcoded states based on encoder position and bumper state.
            Jumps between line sensing and north sensing modes to complete the course.
            """

            if state == S0_wait_to_start:
                line_heading.put(4)
                if button_state != prev_button_state:
                    prev_button_state = button_state
                    sleep(.2)
                    state = S1_to_diamond
            elif button_state != prev_button_state:
                prev_button_state = button_state
                state = S0_wait_to_start

            if state == S1_to_diamond:
                line_heading.put(0)
                if rep == 0:
                    thresh = right_pos.get() + 5_500
                    heading_north = (imu.read_heading()+90)%360
                    print(f'Heading North: {heading_north}')
                    rep += 1

                if right_pos.get() > thresh:
                    state = S2_straightline_diamond
                    rep = 0

            if state == S2_straightline_diamond:

                if rep == 0:
                    line_heading.put(1)
                    hed_set = heading_north + 90

                    if hed_set < 0:
                        hed_set += 360
                    elif hed_set > 360:
                        hed_set -= 360
                    heading_set.put(hed_set)
                    thresh = right_pos.get() + 1_000
                    print(f'Threshold: {thresh}, hed_set: {hed_set}')
                    rep += 1
                if right_pos.get() > thresh:
                    state = S3_to_grid
                    rep = 0
            if state == S3_to_grid:
                line_heading.put(0)
                if rep == 0:
                    thresh = right_pos.get() + 16_000
                    rep += 1
                if right_pos.get() > thresh:
                    state = S4_to_turn
                    rep = 0
            if state == S4_to_turn:
                line_heading.put(1)
                if rep == 0:
                    thresh = right_pos.get() + 4_000
                    hed_set = heading_north - 180
                    if hed_set < 0:
                        hed_set += 360
                    elif hed_set > 360:
                        hed_set -= 360
                    heading_set.put(hed_set)
                    rep += 1
                if right_pos.get() > thresh:
                    state = S5_turn_1
                    right_speed.put(0)
                    left_speed.put(0)
                    rep = 0
            if state == S5_turn_1:
                if rep == 0:
                    hed_set = heading_north - 90
                    if hed_set < 0:
                        hed_set += 360
                    elif hed_set > 360:
                        hed_set -= 360
                    heading_set.put(hed_set)
                    line_heading.put(2)
                    rep += 1
                if -10 < (hed_set - heading.get()) < 10:
                    right_speed.put(0)
                    left_speed.put(0)
                    state = S6_to_wall
                    rep = 0
            if state == S6_to_wall:
                line_heading.put(0)
                if bumper_state:
                    print(f'Bumper hit')
                    right_speed.put(0)
                    left_speed.put(0)
                    state = S7_reverse
            if state == S7_reverse:
                line_heading.put(3)

                if rep == 0:
                    thresh = right_pos.get() - 500
                    hed_set = heading_north - 90

                    if hed_set < 0:
                        hed_set += 360
                    elif hed_set > 360:
                        hed_set -= 360
                    print(f'hed_set: {hed_set}')
                    heading_set.put(hed_set)
                    rep += 1
                if right_pos.get() < thresh:
                    right_speed.put(0)
                    left_speed.put(0)
                    state = S8_turn_2
                    rep = 0
            if state == S8_turn_2:
                line_heading.put(2)
                if rep == 0:
                    hed_set = heading_north
                    if hed_set < 0:
                        hed_set += 360
                    elif hed_set > 360:
                        hed_set -= 360
                    heading_set.put(hed_set)
                    line_heading.put(2)
                    rep += 1
                if -10 < (hed_set - heading.get()) < 10:
                    right_speed.put(0)
                    left_speed.put(0)
                    state = S9_to_3
                    rep = 0
            if state == S9_to_3:
                line_heading.put(1)
                heading_set.put(heading_north)
                if rep == 0:
                    thresh = right_pos.get() + 2_000
                    rep += 1
                if right_pos.get() > thresh:
                    state = S10_turn_3
                    rep = 0
            if state == S10_turn_3:
                line_heading.put(2)
                if rep == 0:
                    hed_set = heading_north - 90
                    if hed_set < 0:
                        hed_set += 360
                    elif hed_set > 360:
                        hed_set -= 360
                    heading_set.put(hed_set)
                    line_heading.put(2)
                    rep += 1
                if -10 < (hed_set - heading.get()) < 10:
                    right_speed.put(0)
                    left_speed.put(0)
                    state = S11_to_4
                    rep = 0
            if state == S11_to_4:
                line_heading.put(1)
                hed_set = heading_north - 90
                if hed_set < 0:
                    hed_set += 360
                elif hed_set > 360:
                    hed_set -= 360
                heading_set.put(hed_set)
                if rep == 0:
                    thresh = right_pos.get() + 2_000
                    rep += 1
                if right_pos.get() > thresh:
                    state = S12_turn_4
                    rep = 0
            if state == S12_turn_4:
                line_heading.put(2)
                if rep == 0:
                    hed_set = heading_north - 180
                    if hed_set < 0:
                        hed_set += 360
                    elif hed_set > 360:
                        hed_set -= 360
                    heading_set.put(hed_set)
                    line_heading.put(2)
                    rep += 1
                if -10 < (hed_set - heading.get()) < 10:
                    right_speed.put(0)
                    left_speed.put(0)
                    state = S13_to_finish
                    rep = 0
            if state == S13_to_finish:
                if rep == 0:
                    hed_set = heading_north - 180
                    if hed_set < 0:
                        hed_set += 360
                    elif hed_set > 360:
                        hed_set -= 360
                    heading_set.put(hed_set)
                    line_heading.put(1)
                    thresh = right_pos.get() + 2_200
                    rep += 1
                if right_pos.get() > thresh:
                    state = S0_wait_to_start
                    rep = 0

                    print('Done!')


    except KeyboardInterrupt:
        print('done hopefully')
    right_speed.put(0)
    right_stop.put(1)
    left_speed.put(0)
    left_stop.put(1)
    # print('\n' + str(cotask.task_list))
    # print(task_share.show_all())
    # print('')
    while True:
        cotask.task_list.pri_sched()
        pass

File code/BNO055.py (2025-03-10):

import time
import struct
from pyb import Pin, I2C
i2c = I2C(3, I2C.CONTROLLER)  # Make sure you're using the correct I2C bus
time.sleep(1)  # Allow devices to power up

devices = i2c.scan()  # Scan for I2C devices
print(f"Detected I2C devices: {devices}")

if not devices:
    print("No I2C devices found")
else:
    print(f"Found I2C devices at addresses: {[hex(dev) for dev in devices]}")



class BNO055:
    """A driver class for the BNO055 IMU using I2C communication."""

    I2C_ADDR = 0x28  # Default I2C address for the BNO055
    #I2C_ADDR=0x29
    OPR_MODE_REG = 0x3D
    CALIB_STAT_REG = 0x35
    EULER_H_LSB_REG = 0x1A
    GYRO_DATA_LSB_REG = 0x14
    CALIB_DATA_REG = 0x55

    CONFIG_MODE = 0x00
    NDOF_MODE = 0x0C  # Sensor fusion mode

    def __init__(self, i2c, reset_pin):
        """
        Initializes the BNO055 sensor.

        :param i2c: An initialized I2C object.
        :param reset_pin: The reset pin (active low).
        """
        self.i2c = i2c
        self.reset_pin = Pin(reset_pin, Pin.OUT_PP)
        self.reset_pin.high()
        self.i2c.mem_write(0x0C,self.I2C_ADDR,0x3D)
        time.sleep(0.75)
        #self.reset()

    def reset(self):
        """Resets the BNO055 using the reset pin."""
        self.reset_pin.low()
        time.sleep(0.01)
        self.reset_pin.high()
        time.sleep(0.75)  # Allow time for reboot

    def set_mode(self, mode):
        """Set the operation mode with retry on failure."""
        self.mode=mode
        self.i2c.mem_write(self.mode,self.I2C_ADDR,0x3D)
        time.sleep(0.05)
        

    def get_calibration_status(self):
        """
        Reads and returns the IMU calibration status.

        :return: A tuple (system, gyroscope, accelerometer, magnetometer) with values 0-3.
        """
        status=self.i2c.mem_read(1,self.I2C_ADDR,0x35)[0]
        bit,=struct.unpack('<B',status)
        system=(bit>>6) & 0x03
        gyro=(bit>>4) & 0x03
        acct=(bit>>2) & 0x03
        magnet=bit & 0x03
        return system,gyro,acct,magnet
        #status = self.i2c.mem_read(1, self.I2C_ADDR, self.CALIB_STAT_REG)[0]
        #return (status >> 6) & 0x03, (status >> 4) & 0x03, (status >> 2) & 0x03, status & 0x03

    def read_euler_angles(self):
        """
        Reads and returns Euler angles (heading, roll, pitch) in degrees.

        :return: A tuple (heading, roll, pitch) in degrees.
        """
        data = self.i2c.mem_read(6, self.I2C_ADDR, 0x1A)
        heading, roll, pitch = struct.unpack('<hhh', data)
        return heading / 16.0, roll / 16.0, pitch / 16.0

    def read_heading(self):
        """
        Reads and returns only the heading angle in degrees.

        :return: Heading in degrees.
        """
        data = self.i2c.mem_read(2, self.I2C_ADDR, 0x1A)
        heading, = struct.unpack('<h', data)
        return heading / 16.0

    def read_angular_velocity(self):
        """
        Reads angular velocity data (gyro X, Y, Z).

        :return: A tuple (gyro_x, gyro_y, gyro_z) in degrees per second.
        """
        data = self.i2c.mem_read(6, self.I2C_ADDR, 0x14)
        gyro_x, gyro_y, gyro_z = struct.unpack('<hhh', data)
        return gyro_x / 16.0, gyro_y / 16.0, gyro_z / 16.0

    def read_yaw_rate(self):
        """
        Reads and returns only the yaw rate from the gyroscope.

        :return: Yaw rate in degrees per second.
        """
        data = self.i2c.mem_read(2, self.I2C_ADDR, 0x18)  # Z-axis gyro
        yaw_rate, = struct.unpack('<h', data)
        return yaw_rate / 16.0

# Example Usage
if __name__ == "__main__":
    i2c = I2C(1, I2C.CONTROLLER) #baudrate=
    imu = BNO055(i2c, "C9")  # Reset pin example
    
    imu.set_mode(BNO055.NDOF_MODE)
    print("Calibration Status:", imu.get_calibration_status())
    print("Euler Angles:", imu.read_euler_angles())
    print("Heading:", imu.read_heading())
    print("Angular Velocity:", imu.read_angular_velocity())
    print("Yaw Rate:", imu.read_yaw_rate())

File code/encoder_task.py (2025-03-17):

from encoder import Encoder

class EncoderTask:
    """
    A class to handle reading the encoder and updating shared variables.

    Attributes
    ----------
    right_enc_A : int
        The pin for channel A for the right wheel encoder.
    right_enc_B : int
        The pin for channel B for the right wheel encoder.
    right_enc_timer : int
        The channel timer number for the right wheel encoder.
    left_enc_A : int
        The pin for channel A for the left wheel encoder.
    left_enc_B : int
        The pin for channel B for the left wheel encoder.
    left_enc_timer : int
        The channel timer number for the left wheel encoder.
    S0_init : int
        Initialization state value.
    S1_init : int
        Read state value.
    state : int
        Current state value.
    right_encoder : Encoder
        Encoder class object for the right wheel encoder.
    left_encoder : Encoder
        Encoder class object for the left wheel encoder.
    """
    def __init__(self, pins):
        """
        Initializes the EncoderTask object and creates Encoder classes for each encoder.

        Parameters
        ----------
        pins : list
            The values for encoder channels and timers.
        """

        right_enc_A = pins[0]
        right_enc_B = pins[1]
        right_enc_timer = pins[2]
        left_enc_A = pins[3]
        left_enc_B = pins[4]
        left_enc_timer = pins[5]
        self.S0_init = 0
        self.S1_read = 1

        self.state = self.S0_init

        self.right_encoder = Encoder(right_enc_A, right_enc_B, right_enc_timer)
        self.left_encoder = Encoder(left_enc_A, left_enc_B, left_enc_timer)
    def encoder_gen(self, shares):
        """
        The generator that implements the finite state machine for the Encoder task.

        State 0 zeros the encoder and moves to state 1. State 1 updates the shares for the
        motor position and velocity for each motor from the `Encoder` class that handles the Encoder.

        Parameters
        ----------
        shares : list[right_pos, right_vel, left_pos, left_vel]
            Shared values for position and velocity for each wheel.

        Yields
        ------
        state : int
            The value of the current state within the machine
        """
        right_pos, right_vel, left_pos, left_vel = shares
        while True:
            # print('in encoder task')
            if self.state == self.S0_init:
                self.right_encoder.zero()  # Reset right encoder
                self.left_encoder.zero()   # Reset left encoder
                self.state = self.S1_read
                yield self.S1_read

            if self.state == self.S1_read:
                self.right_encoder.update()
                self.left_encoder.update()
                # Read right encoder
                right_pos.put(self.right_encoder.get_position())
                right_vel.put(self.right_encoder.get_velocity())
                # Read left encoder
                left_pos.put(self.left_encoder.get_position())
                left_vel.put(self.left_encoder.get_velocity())
                # print(f'Right Pos: {right_pos.get()}')
                yield self.S1_read
                

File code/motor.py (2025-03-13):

from pyb import Pin, Timer
from time import ticks_us, ticks_diff, ticks_add, ticks_ms

class Motor:
    """
    A class to control a DC motor using PWM and direction signals.

    Attributes
    ----------
    pwm_pin : Pin
        Pin object for the PWM signal controlling motor speed.
    dir_pin : Pin
        Pin object for setting the motor direction.
    slp_pin : Pin
        Pin object for enabling or disabling the motor.
    pwm_timer : Timer
        Timer object configured for PWM signal generation.
    pwm_channel : Timer.channel
        Timer channel used for generating the PWM signal.
    kp : float
        Proportional gain for the PID controller.
    ki : float
        Integral gain for the PID controller.
    integral : float
        Integral term accumulation for the PID controller.
    prev_time : int
        Timestamp of the previous PID update.
    del_time : int
        Time difference between PID updates.
    now : int
        Current timestamp for PID calculations.
    prev_error : float
        Previous error value used in the PID controller.
    """
    def __init__(self, pins, pwm_channel, gains):
        self.pwm_pin = Pin(pins[0], mode=Pin.OUT_PP)
        self.dir_pin = Pin(pins[1], mode=Pin.OUT_PP)
        self.slp_pin = Pin(pins[2], mode=Pin.OUT_PP)

        self.pwm_timer = Timer(pins[3], freq=22000, prescaler=0)
        self.pwm_channel = self.pwm_timer.channel(pwm_channel, Timer.PWM, pin=self.pwm_pin)

        self.kp, self.ki = gains
        self.integral = 0
        self.prev_time = ticks_ms()
        self.del_time = 0
        self.now = ticks_ms()
        self.prev_error = 0



    def forward(self, speed):
        """
        Moves the motor forward at a specified speed.

        Parameters
        ----------
        speed : int
            Speed percentage (0-100) to apply to the motor.
        """
        self.dir_pin.low()
        self.slp_pin.high()
        self.pwm_channel.pulse_width_percent(speed)

    def reverse(self, speed):
        """
        Moves the motor in reverse at a specified speed.

        Parameters
        ----------
        speed : int
            Speed percentage (0-100) to apply to the motor.
        """
        self.dir_pin.high()
        self.slp_pin.high()
        self.pwm_channel.pulse_width_percent(speed)

    def stop(self):
        """
        Stops the motor by setting PWM to 0 while keeping it enabled.
        """
        self.pwm_channel.pulse_width_percent(0)
        self.slp_pin.high()

    def enable(self):
        """
        Enables the motor by setting sleep pin high while keeping PWM at 0.
        """
        self.pwm_channel.pulse_width_percent(0)
        self.slp_pin.high()

    def disable(self):
        """
        Disables the motor by setting the sleep pin low.
        """
        self.pwm_channel.pulse_width_percent(0)
        self.slp_pin.low()

    def pid(self, des, act, vel, mode):
        """
        Implements a PID controller to adjust motor speed based on error.

        Parameters
        ----------
        des : float
            Desired position or velocity.
        act : float
            Actual measured position or velocity.
        vel : int
            Base velocity adjustment value.
        mode : int
            Control mode (0 for standard PID control, 1 for inverse correction).
        """
        error = des - act
        self.now = ticks_ms()
        self.del_time = ticks_diff(self.now, self.prev_time)
        self.integral += (error - self.prev_error) * (self.del_time / 1000)

        output = int(self.kp * error) + self.ki * self.integral
        if mode == 0:
            if output >= 0:
                self.forward(output)
            elif output < 0:
                self.reverse(-output)
        elif mode == 1:
            if output >= 0:
                self.forward(-output)
            elif output < 0:
                self.reverse(output)

        self.prev_error = error
        self.prev_time = self.now

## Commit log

2025-03-07 add current code
2025-03-10 add sensor mount assembly
    [Front Bump Sensor Mount^Romi Assembly.STL, Side Bump Sensor Mount^Romi Assembly.STL]
2025-03-11 updating pages and configurating github pages
    [Front Bump Sensor Mount^Romi Assembly.STL, Side Bump Sensor Mount^Romi Assembly.STL]
2025-03-13 update and fix small errors
    added some stuff to deal with initial imu calibration value
    [control_task.py, heading_task.py, main.py]
2025-03-13 clean up organization
    [Front Bump Sensor Mount^Romi Assembly.STL, Side Bump Sensor Mount^Romi Assembly.STL]
2025-03-15 work on pages
    [Front Bump Sensor Mount.SLDPRT, Front Bump Sensor Mount.STL, Front Bump Sensor Mount^Romi Assembly.STL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]
2025-03-17 add motor parameterization and updated control diagram
2025-03-17 add docstrings to control task, motor task and qtr task
2025-03-17 adjust to fix build errors
    [qtr_sensor.py]
2025-03-17 couple fixes to sizing
